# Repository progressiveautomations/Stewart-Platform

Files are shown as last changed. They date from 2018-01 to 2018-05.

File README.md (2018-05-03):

# Stewart Platform

## Table of Contents
[Quick Start Guide](#qsg)

[Wiring the Electronics](#wiring)

[Mechanical Assembly](#mech)

[Troubleshooting](#ts)

<a name="qsg"/>

# Quick Start Guide
1. Ensure that power to the platform is turned off, the USB cable from the platform is unplugged from the computer, and all GUI instances are closed.
2. (if Leap Motion is to be used) Ensure that the Leap Motion service and software is started, and the controller is plugged into the computer.
3. Turn on the power to the platform, and plug the USB cable from the platform into the computer.
4. Launch the GUI; in the 'Options' menu, click "Select COM Port".
5. Find the COM port corresponding to the Arduino Due (should show up in the Device Description on the left hand side, as shown), and change the baud rate to 115200.
6. Click connect, and the platform should immediately begin its calibration routine by moving all actuators to full extension, and retracting to minimum position. DO NOT SEND ANY COMMANDS TO THE PLATFORM DURING THIS PHASE!
7. Check the beginning of the log to ensure calibration has succeeded.
8. Manually control the actuators by moving the sliders and/or entering values into the corresponding textbox. To enable Leap Motion, ensure its status is "Connected", and tick the "Enable Leap Motion" checkbox above the sliders.

# Assembly Instructions

<a name="wiring"/>

## Wiring the Electronics

Before assembly, ensure that all the wires are adequately connected within the enclosure, including the power supply wires, the actuator power wires, the actuator signal wires, and the Arduino Due wires. Detail in [how the components are wired together](electronics/electronics_layout.pdf) and individual schematics are located in the `electronics` folder.

To ensure the code under `arduino/platform` is compatible with the wiring of the Arduino Due, the headers on the PCB should be connected to the respective pins in the table below. This assumes actuators 1 through 3 are connected to Multimoto 1 (to blocks M3, M2, and M1 respectively) and actuators 4 through 6 similarly to Multimoto 2. Note the actuator indexing for the PCBs differs from that in software.
- The indexing on the PCBs are ordered by the motor blocks on the Multimoto boards. Indices 1 through 4 correspond to M1 through M4 on Multimoto 1, and the same for indices 5 though 8 with Multimoto 2.
- The indexing in software is ordered by how the signal wires interface with the PCB terminal blocks. This should match the order (left to right) in which they are connected to the enclosure ports.

The UTIL pin headers (RESET, +3.3V, +5V, GND, GND, Vin) are connected to the identically-named Arduino pins and are omitted from this list. The exact pin numbering can be updated in software at `arduino/platform/pin_layout.h` if the wiring configuration needs to be modified.

| Header | Pin |
|---|----:|
| POT_1 |  A6 |
| POT_2 |  A7 |
| POT_3 |  A8 |
| POT_4 |  A9 |
| POT_5 | A10 |
| POT_6 | A11 |
| DIR_1 |  41 |
| DIR_2 |  39 |
| DIR_3 |  37 |
| DIR_5 |  35 |
| DIR_6 |  33 |
| DIR_7 |  31 |
| PWM_1 |  13 |
| PWM_2 |  12 |
| PWM_3 |  11 |
| PWM_5 |  10 |
| PWM_6 | 9 |
| PWM_7 | 8 |
| ENABLE_1 |  24 |
| ENABLE_2 |  25 |

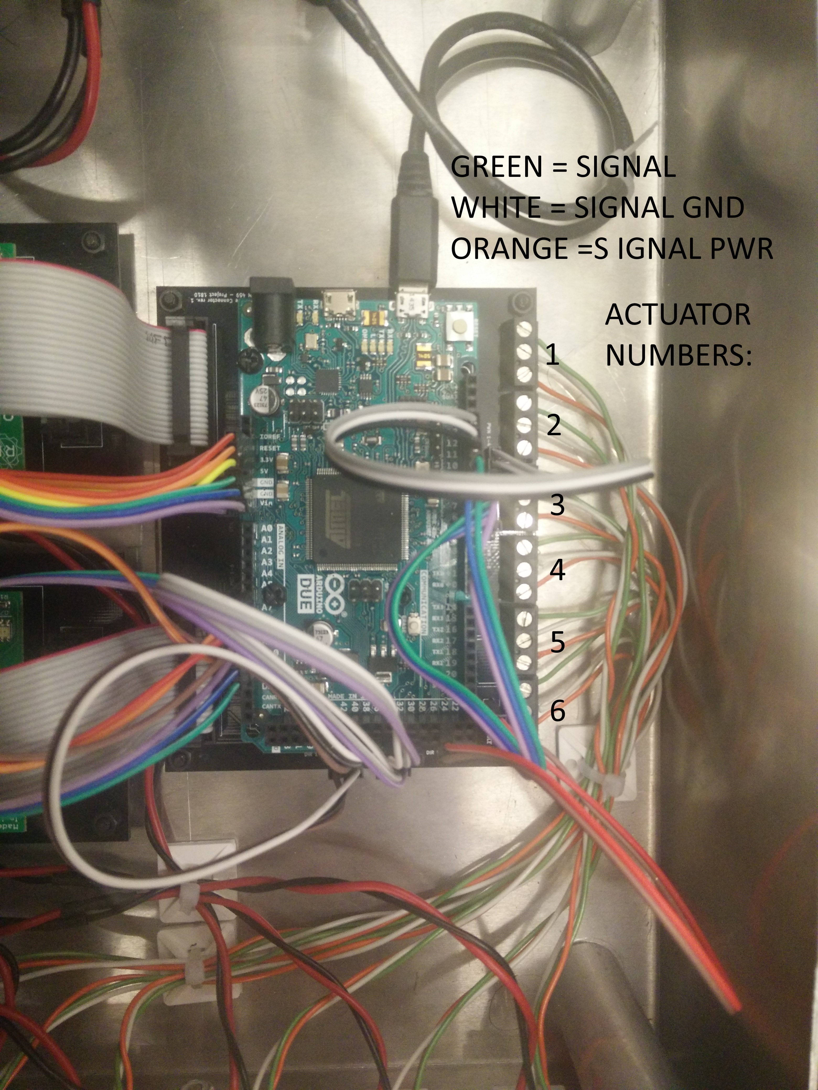
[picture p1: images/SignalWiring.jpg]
Picture of Arduino I/O wiring

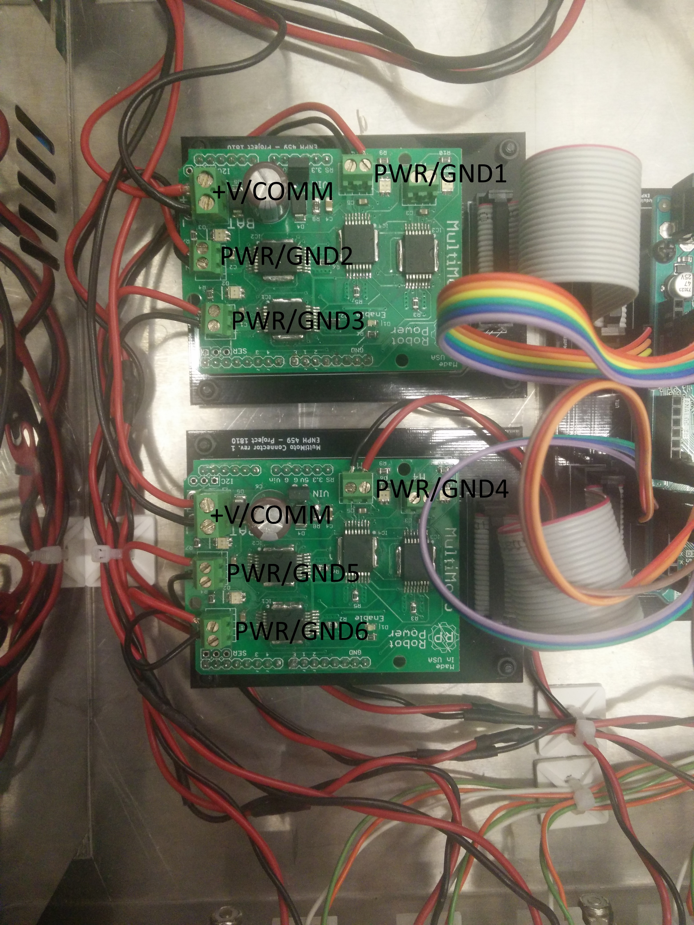
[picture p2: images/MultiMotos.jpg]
Picture of MultiMoto wiring


<a name="mech"/>

## Mechanical Assembly

Attach the 3 platform legs to the 3 corners of the base plate (Note: the base plate is larger than the top plate, and has 4 slots cut into it.), such that the 6 metal flanges are facing upwards. This is done using the ¾” long, ⅜”-16 threaded bolts, with one washer.

Picture of base leg

Next, position the enclosure underneath the base, so that the enclosure posts align with the slots in the base plate, with the power and USB connectors facing out as shown.

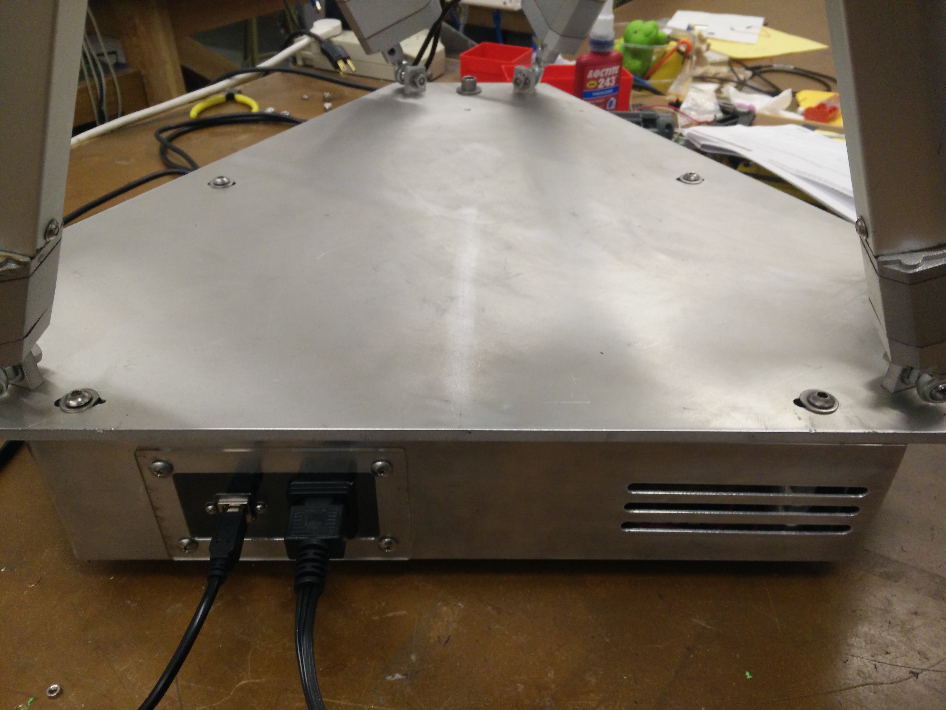
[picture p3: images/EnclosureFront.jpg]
Enclosure picture


Attach the enclosure to the base place using 4 1” long,  ¼”-20 threaded bolts, with a washer for each. Ensure the bolts are aligned in the slots such that the corners of the enclosure do not extend beyond the edge of the base plates, like shown.

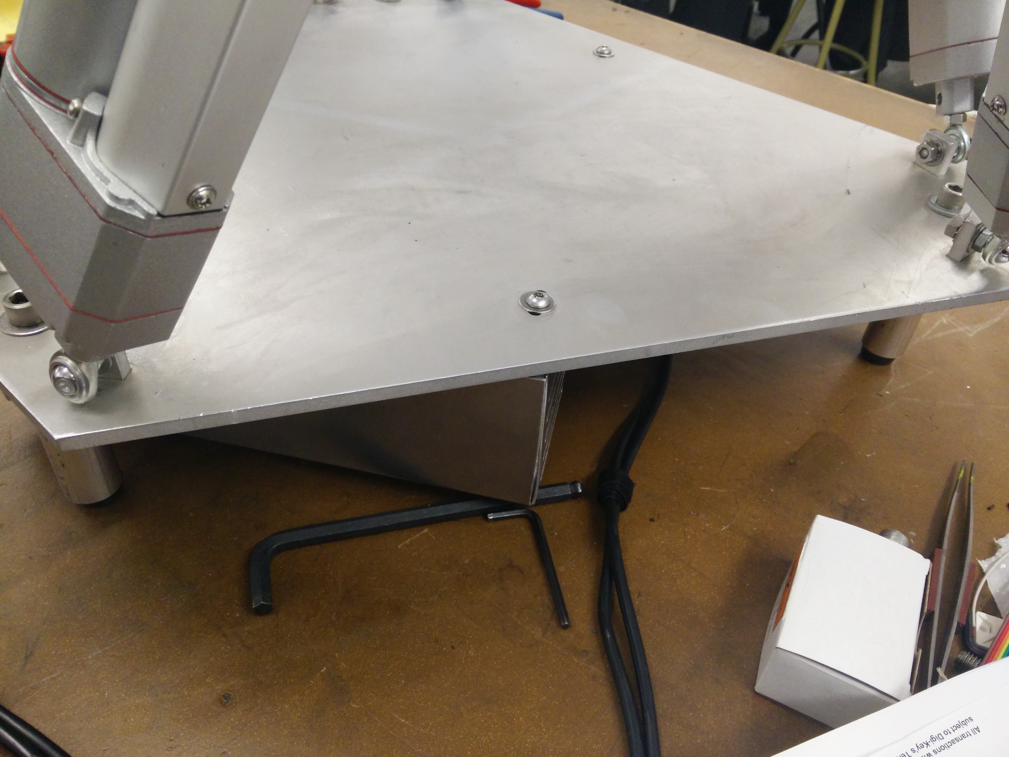
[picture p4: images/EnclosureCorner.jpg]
Enclosure corner


Attach the actuators as shown in the following picture. Close-up views of the joints are provided. Use 2 washers (one on each side), a lock-washer, and a ¼”-28 nut.

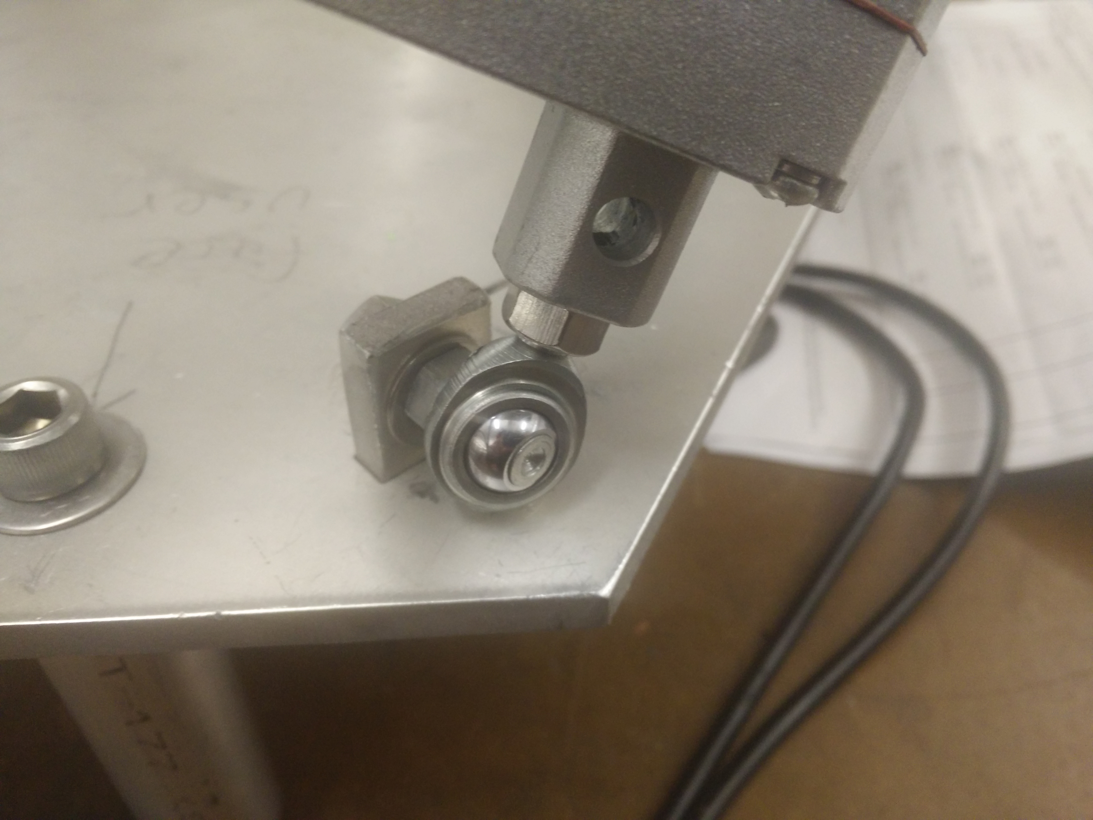
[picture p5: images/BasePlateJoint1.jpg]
Joint picture 1


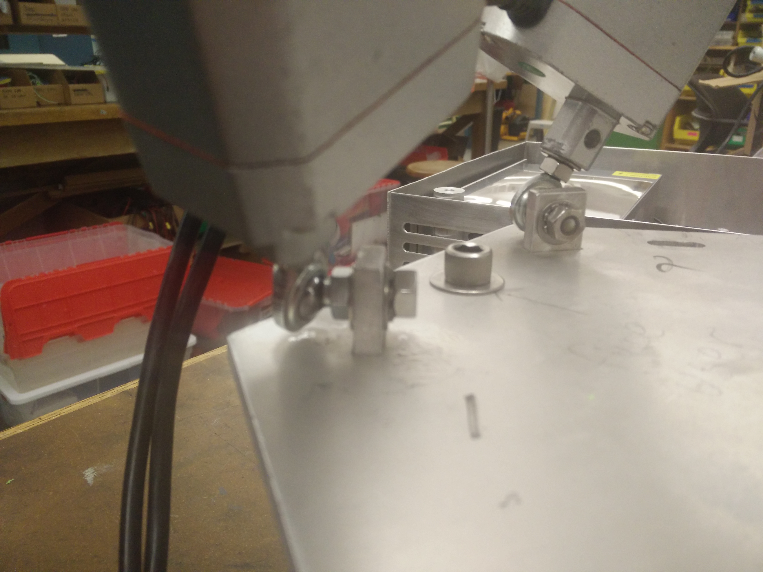
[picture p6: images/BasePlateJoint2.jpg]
Joint picture 2


To avoid problems, ensure that the actuator gearboxes are facing upwards as shown in the picture.

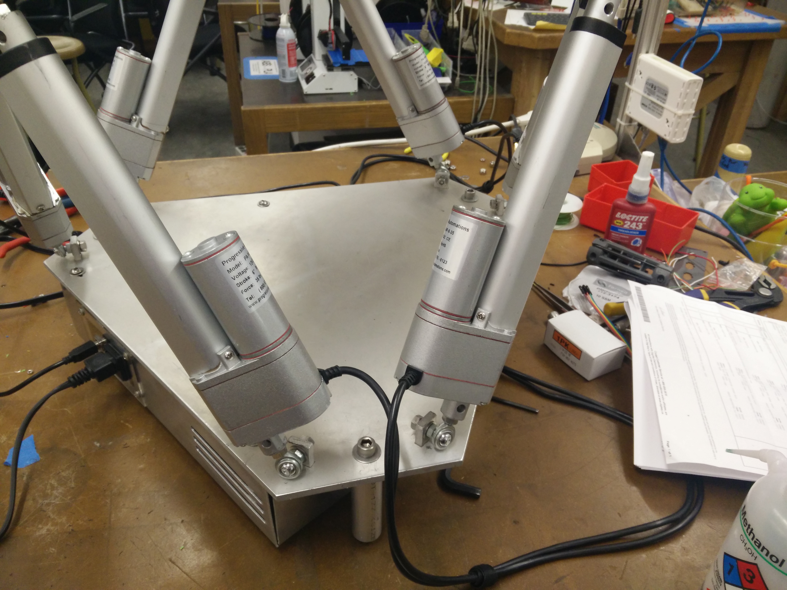
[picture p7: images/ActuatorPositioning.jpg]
Picture of actuator positions


Once the platform is assembled, attach the maze to the top plate by aligning the 3 corner holes on each, and secure it with 3 1¼” long, ⅜”-16 threaded bolts, with one washer on each, and a nut.

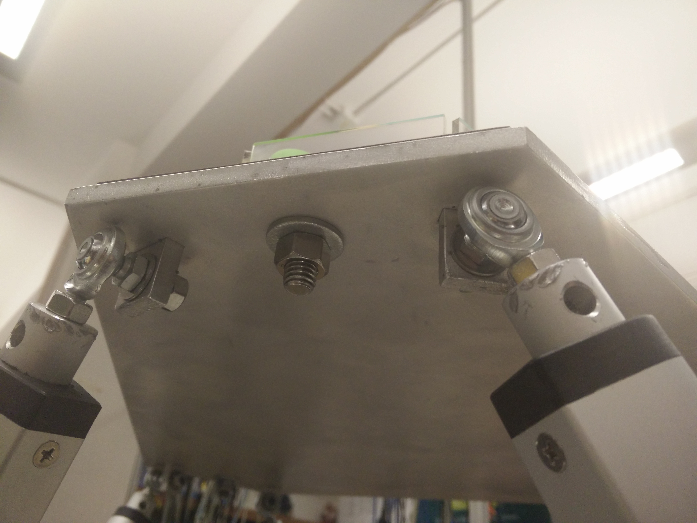
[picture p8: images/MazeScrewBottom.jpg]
Maze bolt pic 1

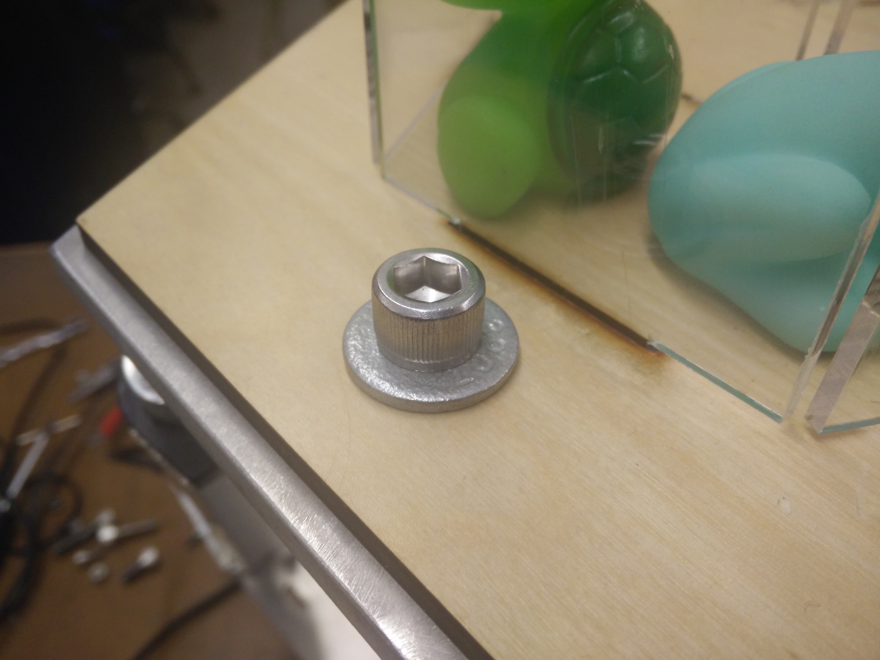
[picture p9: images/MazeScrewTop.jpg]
Maze bolt pic 2


Connect all the actuator connectors to the appropriate receptacles on the enclosure, by routing the cables around and under the base plate. These can be bundled to be neat and out-of-view.

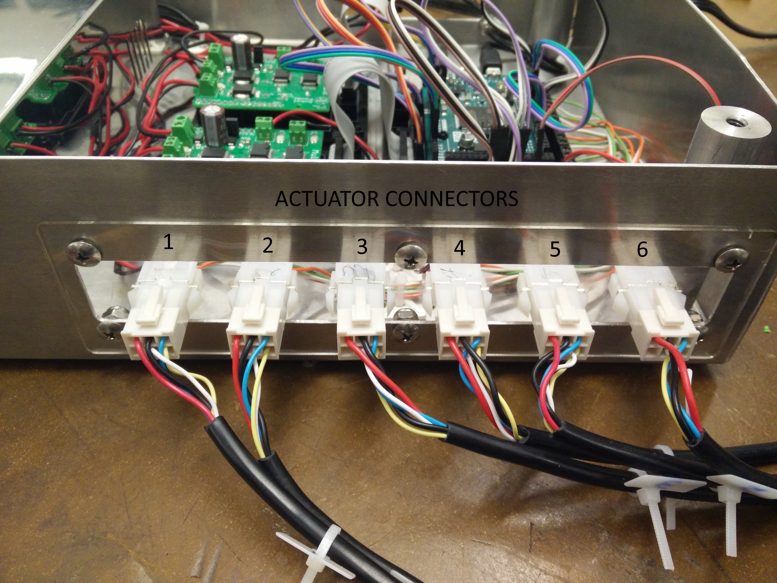
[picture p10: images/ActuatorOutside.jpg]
Pic of cables and connectors


Finally, connect the power and USB cables to the front of the enclosure, and connect the other end of the USB cable. The platform is now assembled!

<a name="ts"/>

# Troubleshooting

Nothing is moving? Check all power connectors.

Arduino not seen by computer? Check USB cable connection, and ensure the device shows up in Device Manager.

Noisy actuator readings? Adjust the PWM feedback or the filtering capacitances on the Arduino PCB.

## PCB design
The PCBs were designed using [KiCAD v4.0.7](http://kicad-pcb.org/).

Each board has its design files under the `electronics` folder, along with Gerber files (under `electronics/gerber`) for the case of reproduction. The individual netlists can be found in the `.sch` files.

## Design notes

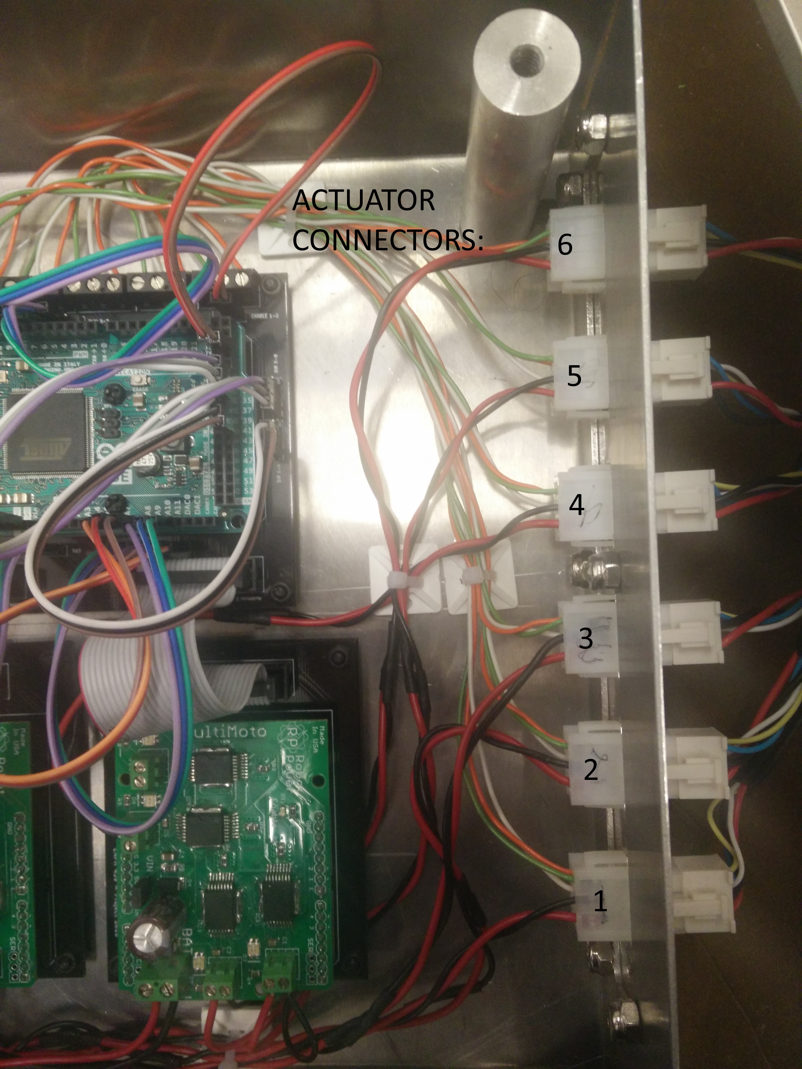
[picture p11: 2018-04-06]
images/ActuatorConnectors.jpg

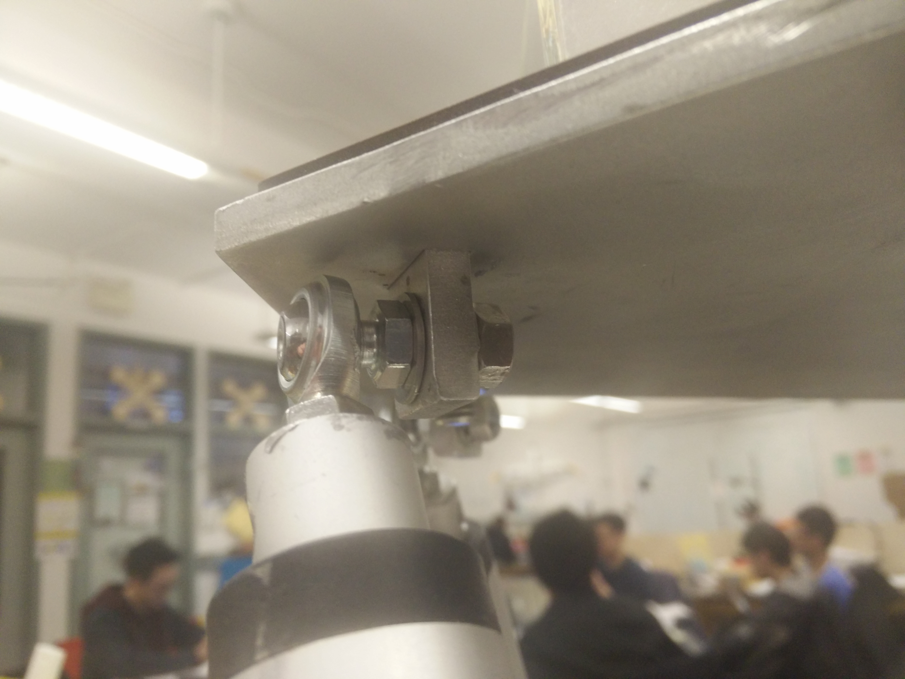
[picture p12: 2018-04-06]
images/TopPlateJoint2.jpg

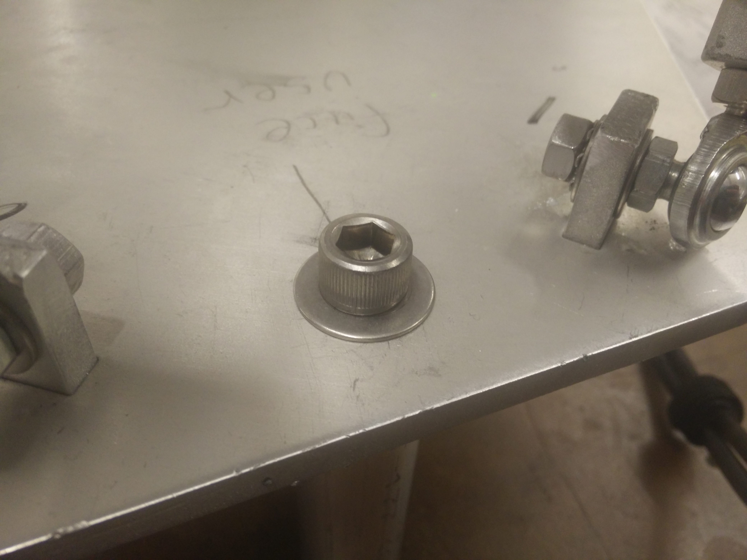
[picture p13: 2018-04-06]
images/BaseScrew.jpg

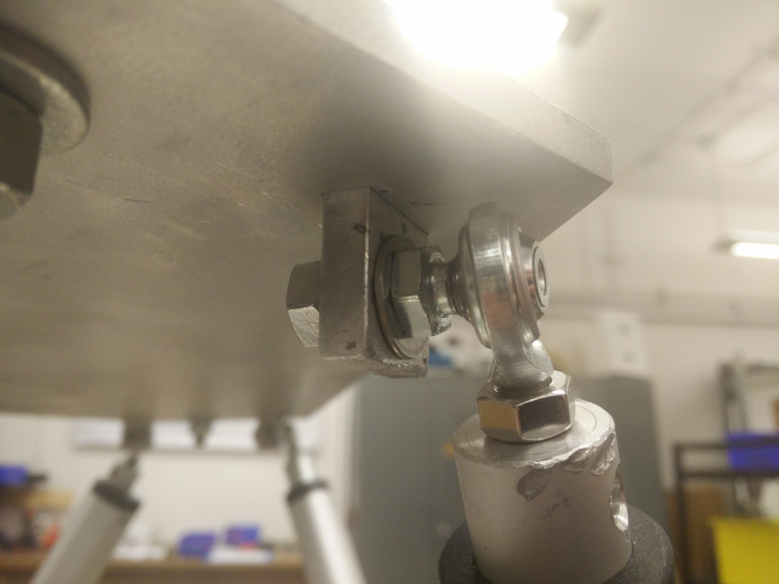
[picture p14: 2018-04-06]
images/TopPlateJoint.jpg

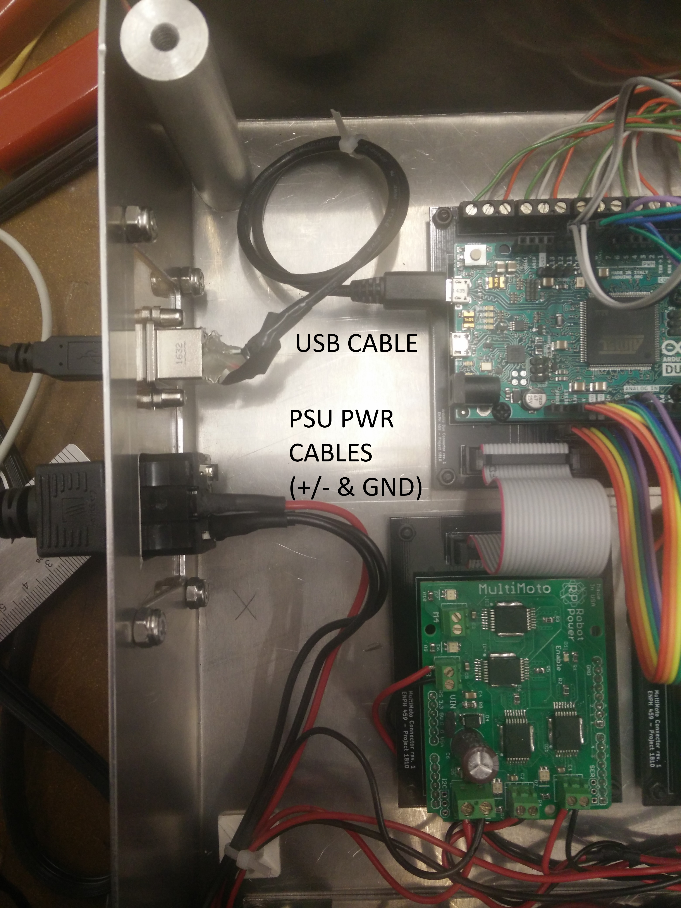
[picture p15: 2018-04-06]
images/USB-PWR.jpg

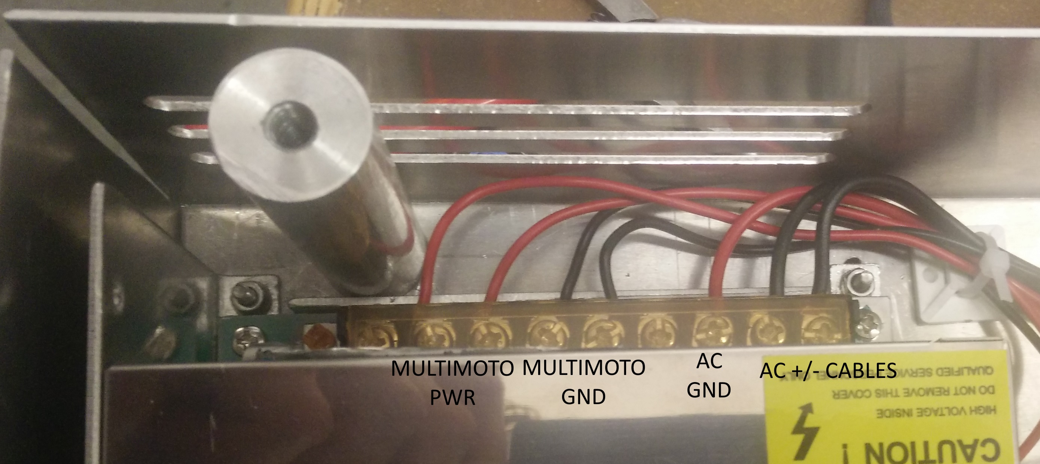
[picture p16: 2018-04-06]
images/PSUCables.jpg

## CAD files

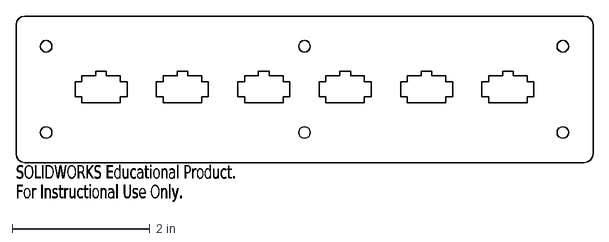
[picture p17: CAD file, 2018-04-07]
mechanical/MotorPanel2.DXF
SOLIDWORKS Educational Product.
For Instructional Use Only.

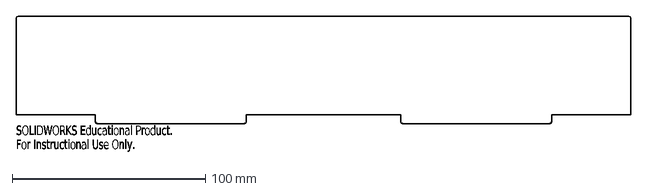
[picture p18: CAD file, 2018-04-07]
mechanical/TiltMazeWallLarge.DXF
SOLIDWORKS Educational Product.
For Instructional Use Only.

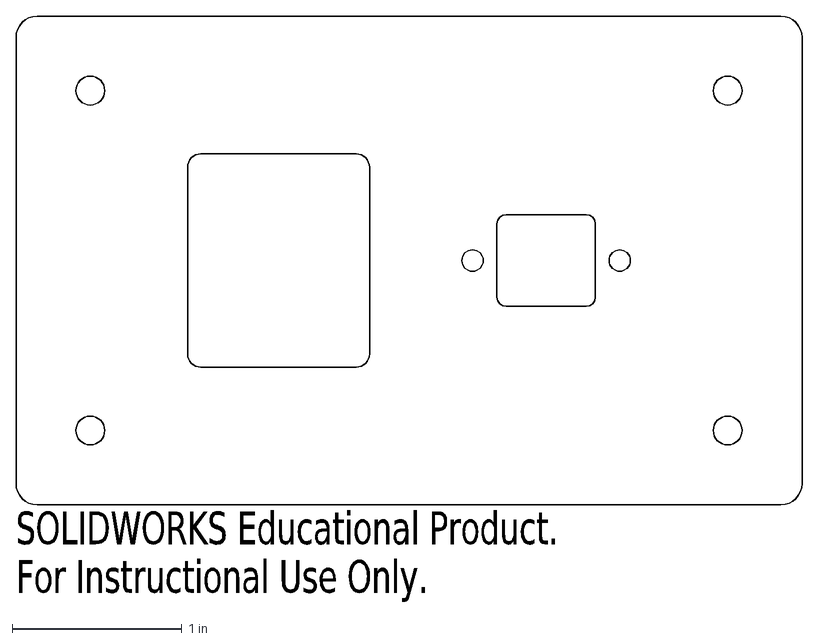
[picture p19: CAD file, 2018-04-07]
mechanical/PowerUSBPanel2.DXF
SOLIDWORKS Educational Product.
For Instructional Use Only.

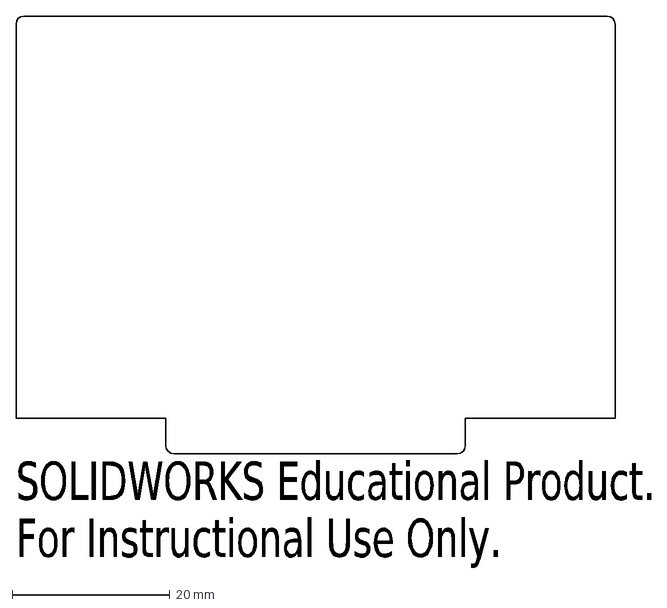
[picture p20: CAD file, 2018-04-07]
mechanical/TiltMazeWallSmall.DXF
SOLIDWORKS Educational Product.
For Instructional Use Only.

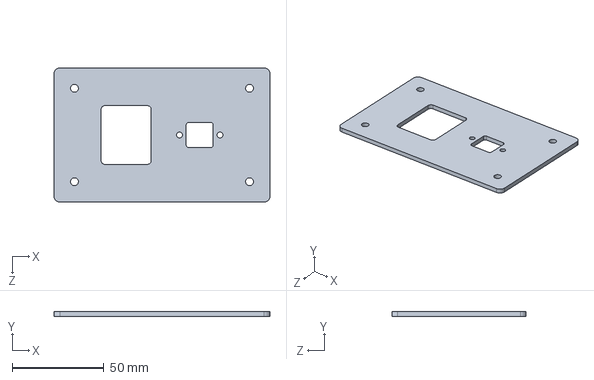
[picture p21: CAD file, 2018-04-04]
mechanical/PowerUSBPanel.SLDPRT
117.5 x 2.54 x 73.0 mm

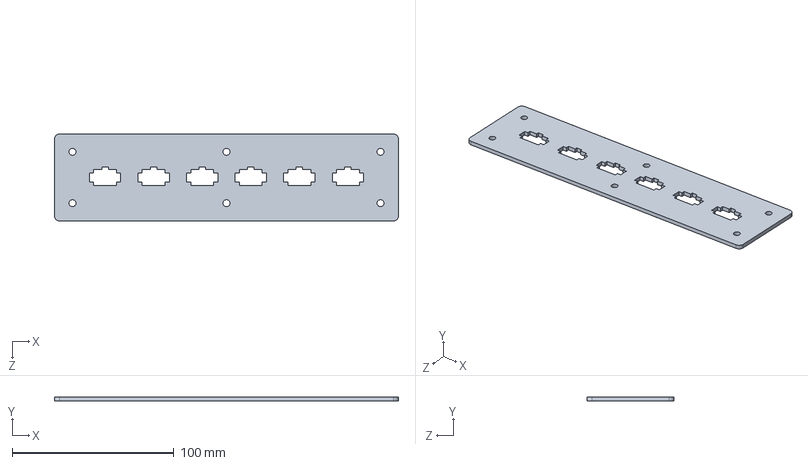
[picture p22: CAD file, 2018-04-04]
mechanical/MotorPanel.SLDPRT
212.7 x 2.54 x 54.0 mm

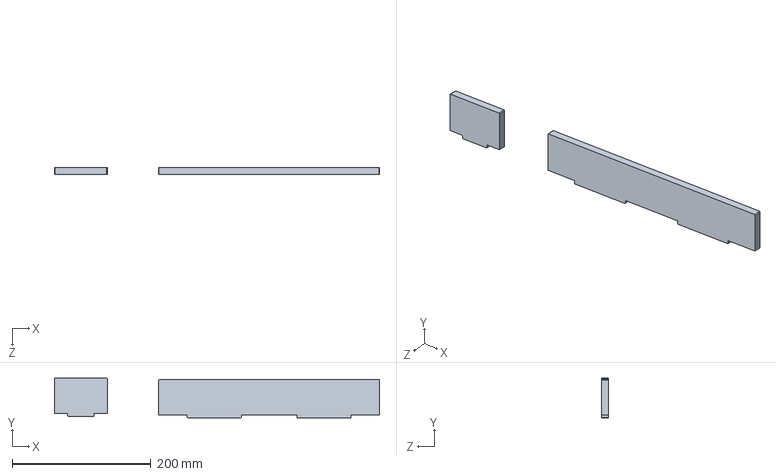
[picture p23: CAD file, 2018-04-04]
mechanical/TiltMazeWalls.SLDPRT
468.1 x 57.6 x 10.0 mm

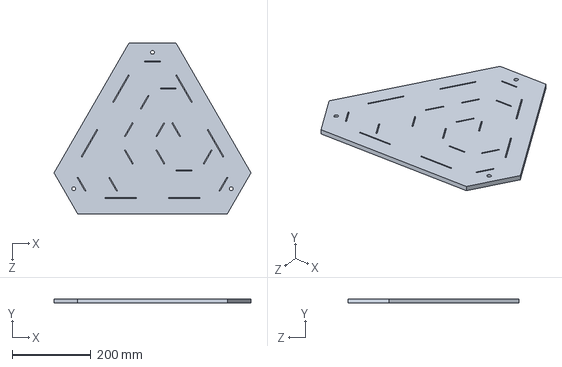
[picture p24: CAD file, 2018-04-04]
mechanical/TiltMaze1.SLDPRT
500.0 x 10.0 x 433.0 mm

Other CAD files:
mechanical/PlatformPlates.SLDPRT
mechanical/MotorPanel.SLDDRW
mechanical/PlatformPlates.SLDDRW
mechanical/PowerUSBPanel.SLDDRW
mechanical/TiltMaze1.DXF
mechanical/TiltMazeBase.SLDDRW
mechanical/TiltMazeWalls.SLDDRW

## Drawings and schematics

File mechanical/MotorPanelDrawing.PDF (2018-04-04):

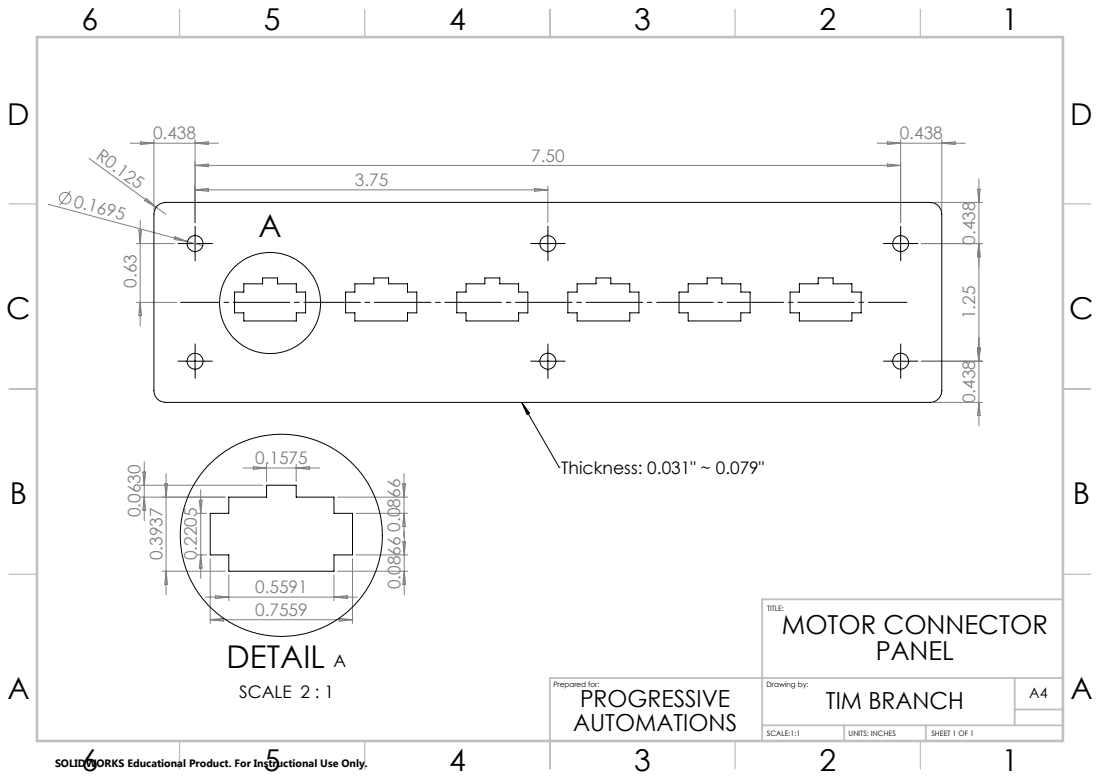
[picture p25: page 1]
Thickness: 0.031" ~ 0.079"; DETAIL A; SCALE 2 : 1; Drawing by:; SCALE:1:1; SHEET 1 OF 1; MOTOR CONNECTOR; TIM BRANCH; Prepared for:; AUTOMATIONS; UNITS: INCHES

SOLIDWORKS Educational Product. For Instructional Use Only.

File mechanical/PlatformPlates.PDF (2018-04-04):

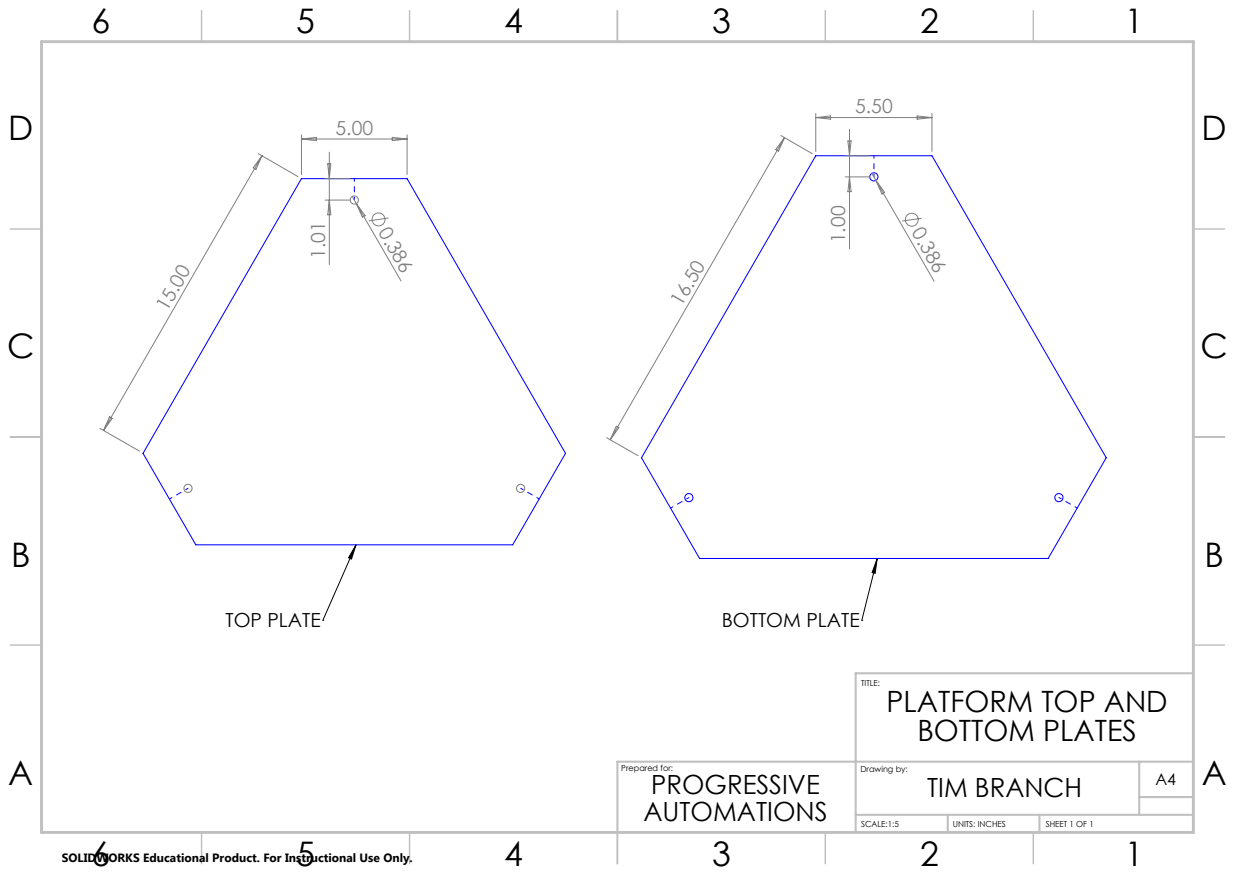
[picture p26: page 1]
TOP PLATE; BOTTOM PLATE; Drawing by:; SCALE:1:5; SHEET 1 OF 1; Prepared for:; AUTOMATIONS; UNITS: INCHES

TITLE:
PLATFORM TOP AND
BOTTOM PLATES
TIM BRANCH

SOLIDWORKS Educational Product. For Instructional Use Only.

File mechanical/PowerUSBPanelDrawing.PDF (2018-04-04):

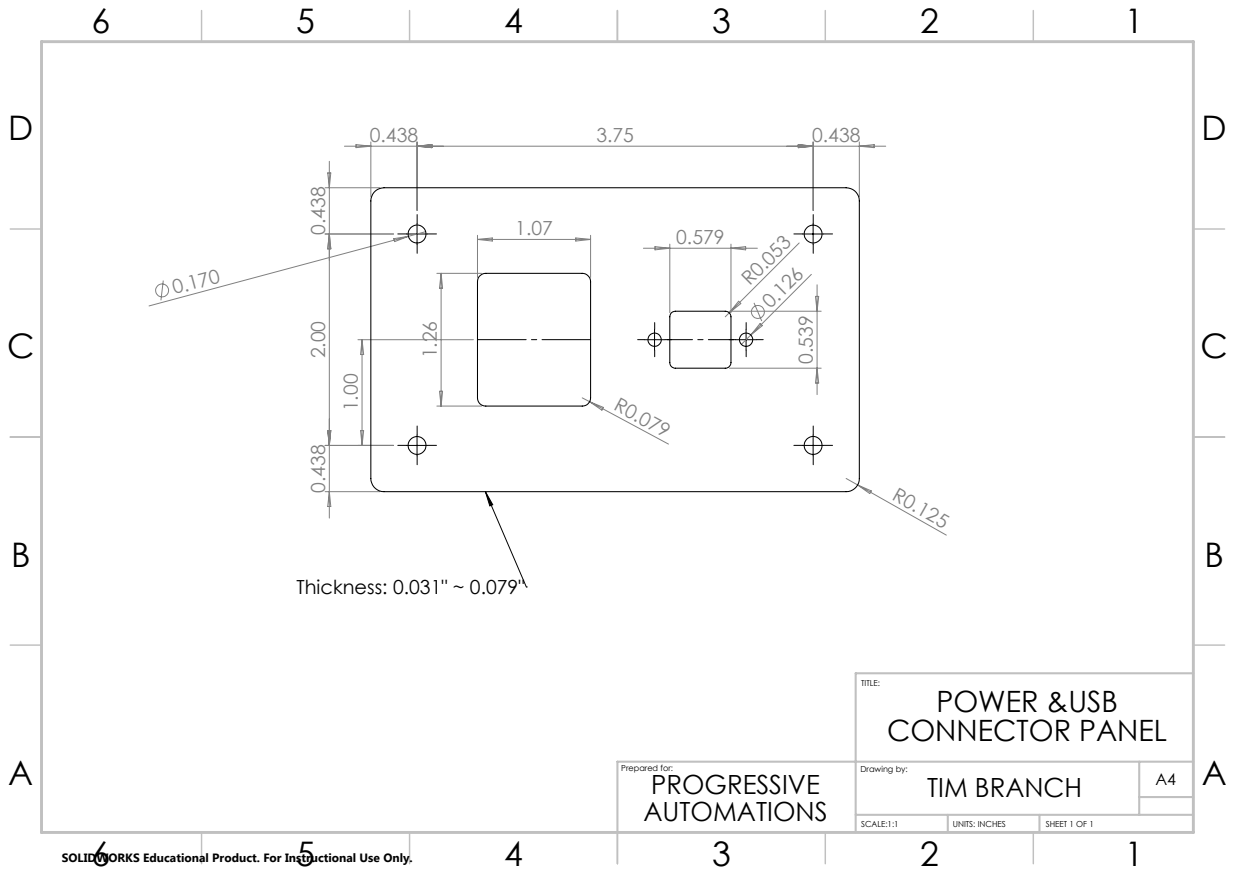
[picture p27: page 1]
Thickness: 0.031" ~ 0.079"; Drawing by:; SCALE:1:1; SHEET 1 OF 1; POWER &USB CONNECTOR PANEL; TIM BRANCH; Prepared for:; AUTOMATIONS; UNITS: INCHES

SOLIDWORKS Educational Product. For Instructional Use Only.

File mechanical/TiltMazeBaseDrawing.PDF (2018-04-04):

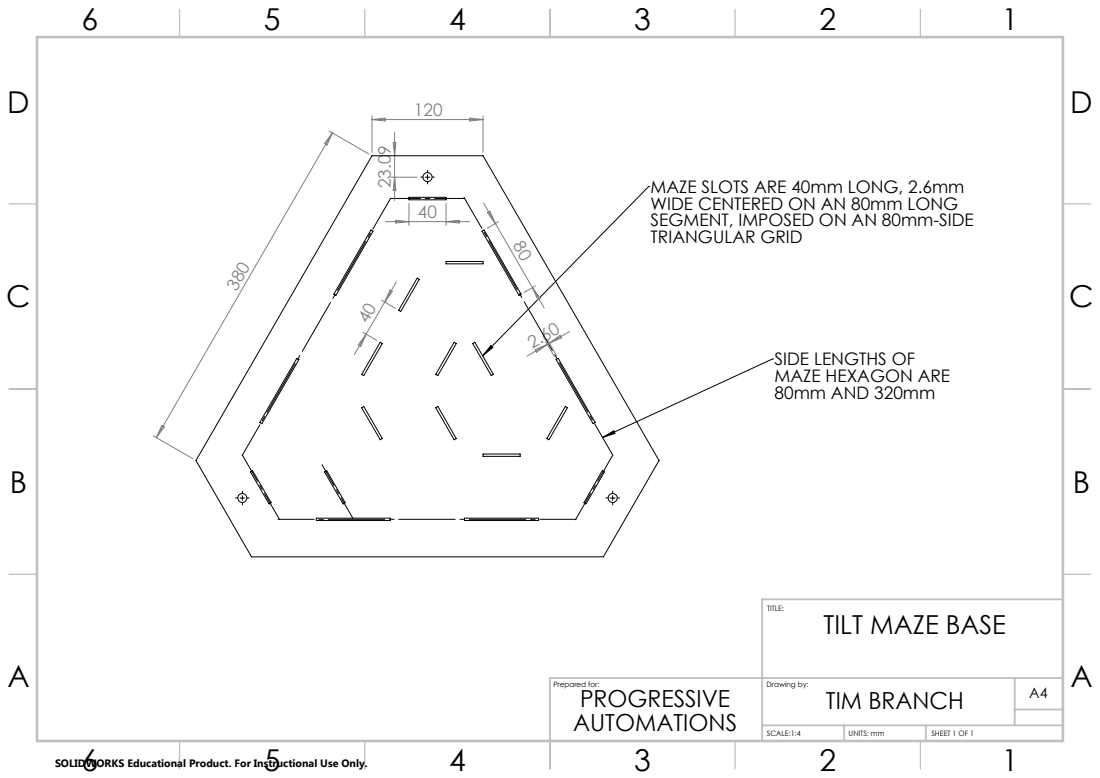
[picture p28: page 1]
Drawing by:; SCALE:1:4; SHEET 1 OF 1; TIM BRANCH; Prepared for:; AUTOMATIONS; UNITS: mm

MAZE SLOTS ARE 40mm LONG, 2.6mm
WIDE CENTERED ON AN 80mm LONG
SEGMENT, IMPOSED ON AN 80mm-SIDE
TRIANGULAR GRID

SIDE LENGTHS OF
MAZE HEXAGON ARE
80mm AND 320mm

TITLE:
TILT MAZE BASE

SOLIDWORKS Educational Product. For Instructional Use Only.

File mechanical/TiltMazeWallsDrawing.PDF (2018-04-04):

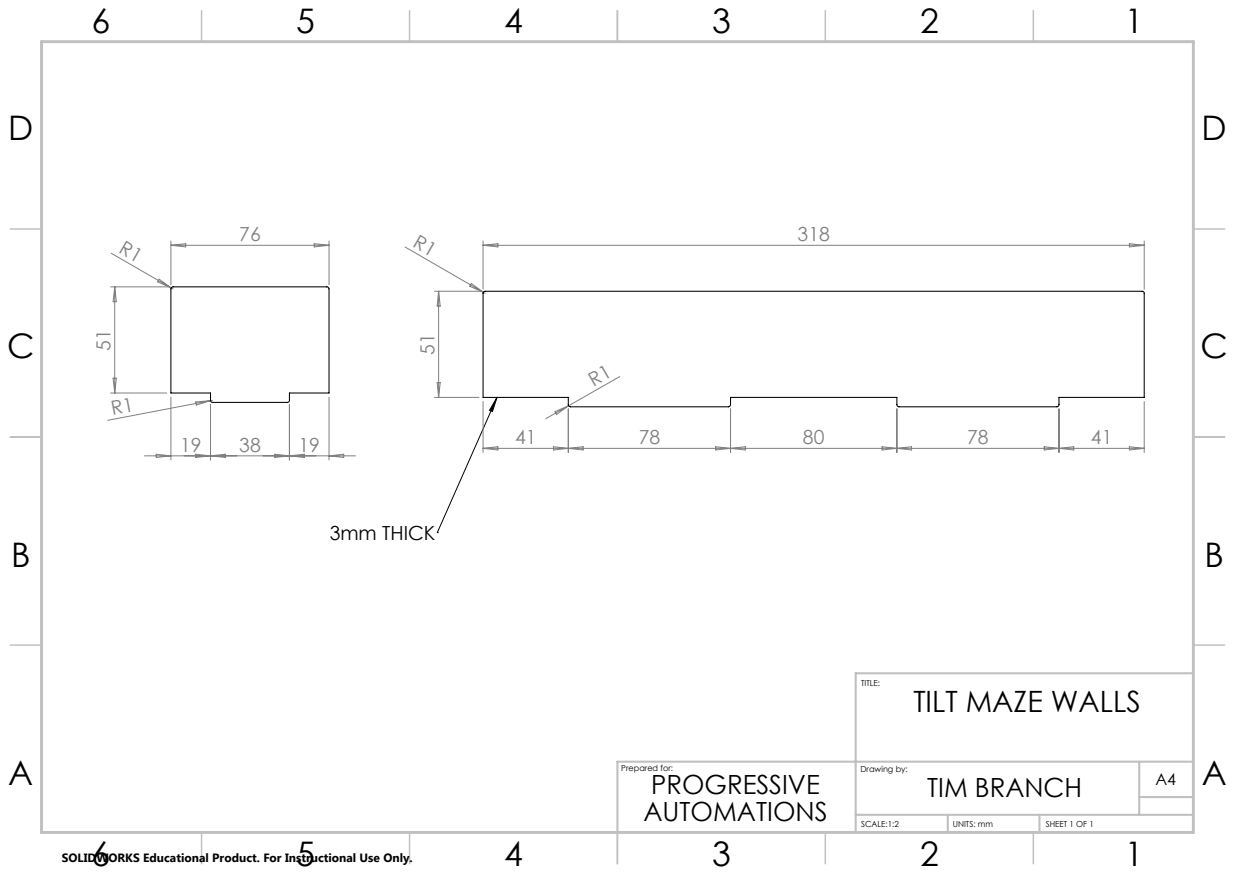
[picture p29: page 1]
3mm THICK; Drawing by:; SCALE:1:2; SHEET 1 OF 1; TIM BRANCH; Prepared for:; AUTOMATIONS; UNITS: mm

TITLE:
TILT MAZE WALLS

SOLIDWORKS Educational Product. For Instructional Use Only.

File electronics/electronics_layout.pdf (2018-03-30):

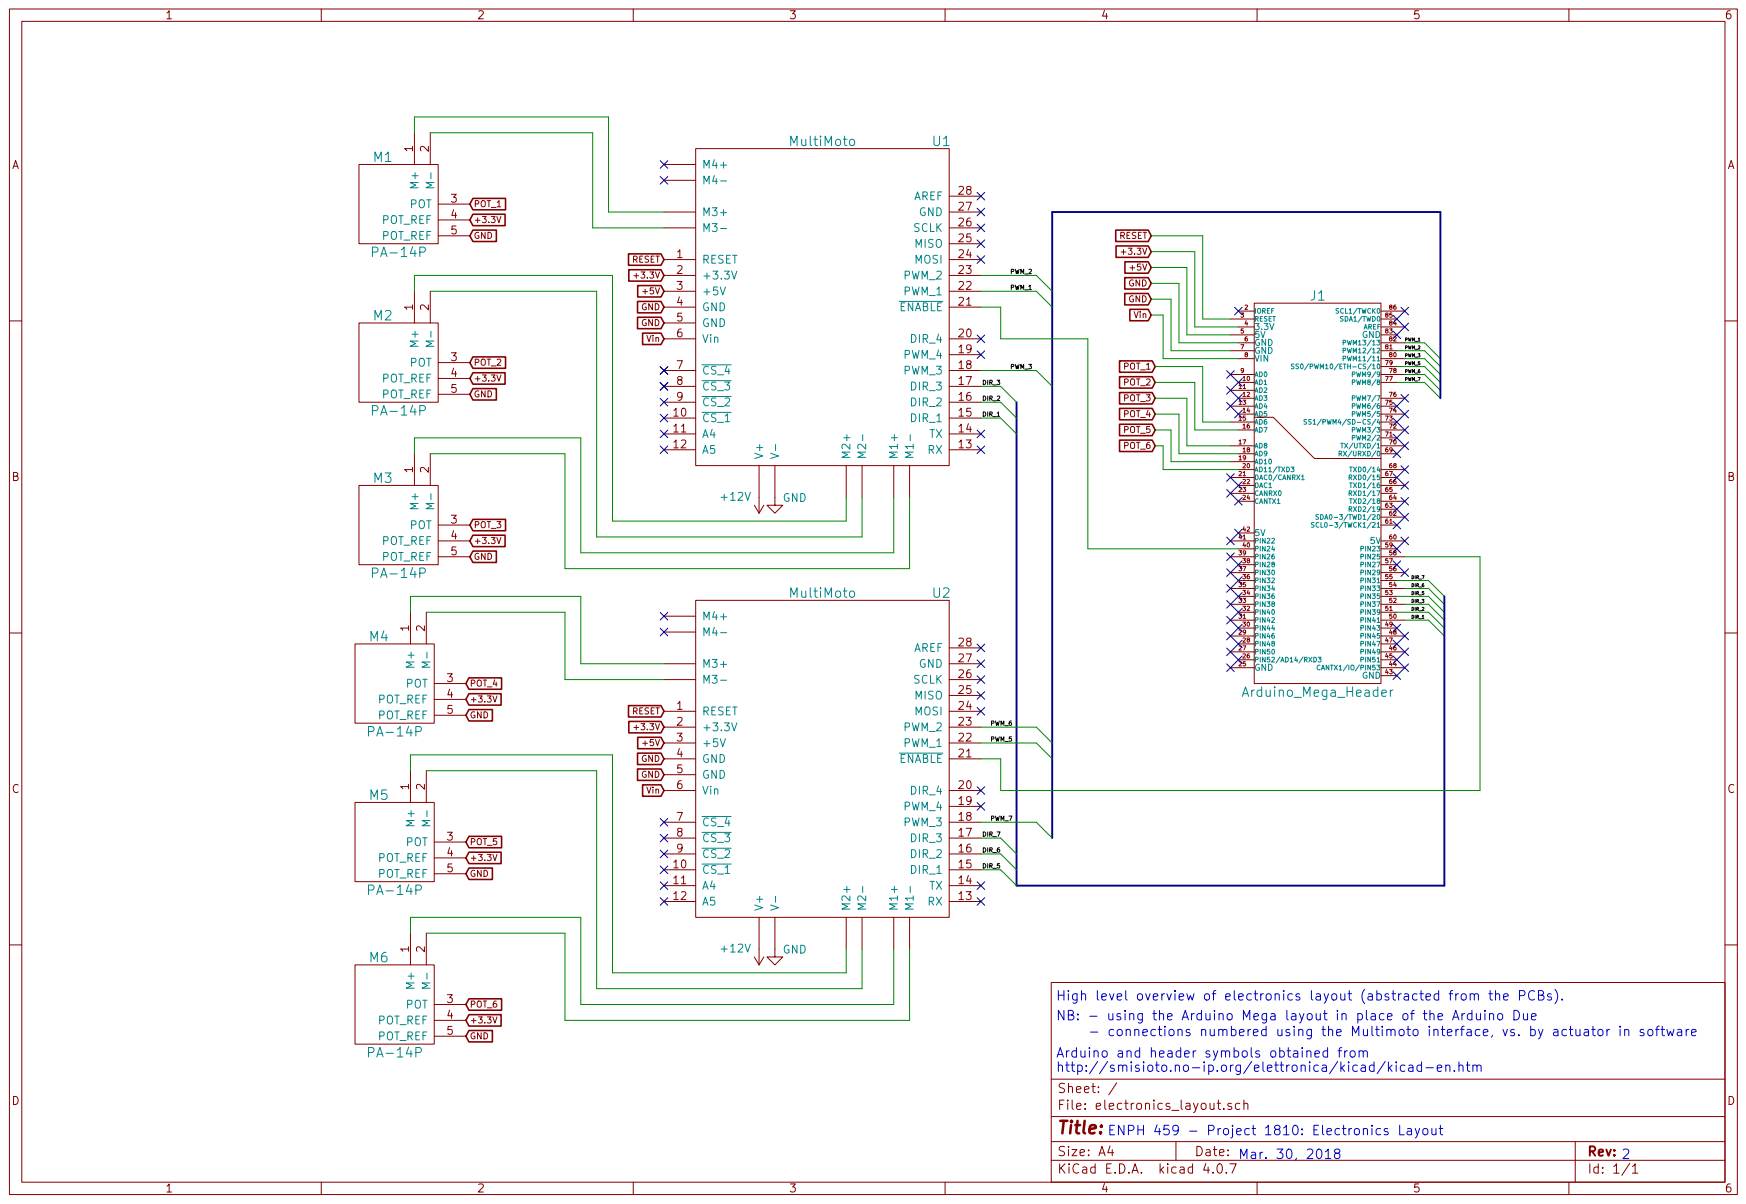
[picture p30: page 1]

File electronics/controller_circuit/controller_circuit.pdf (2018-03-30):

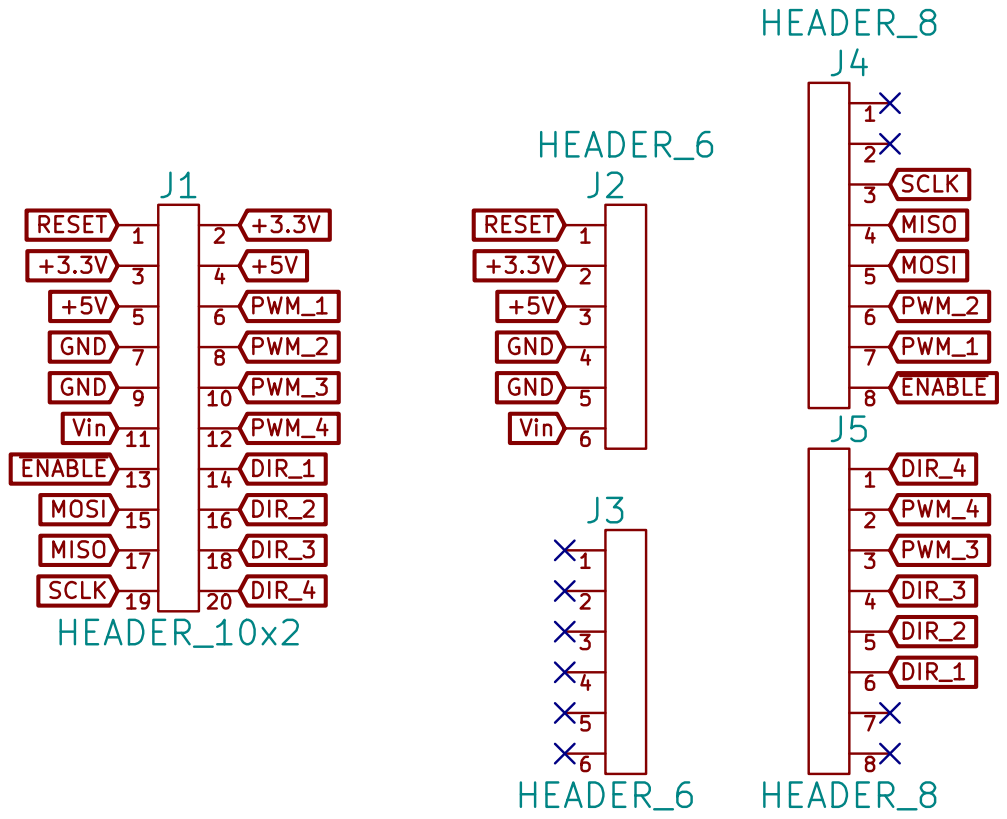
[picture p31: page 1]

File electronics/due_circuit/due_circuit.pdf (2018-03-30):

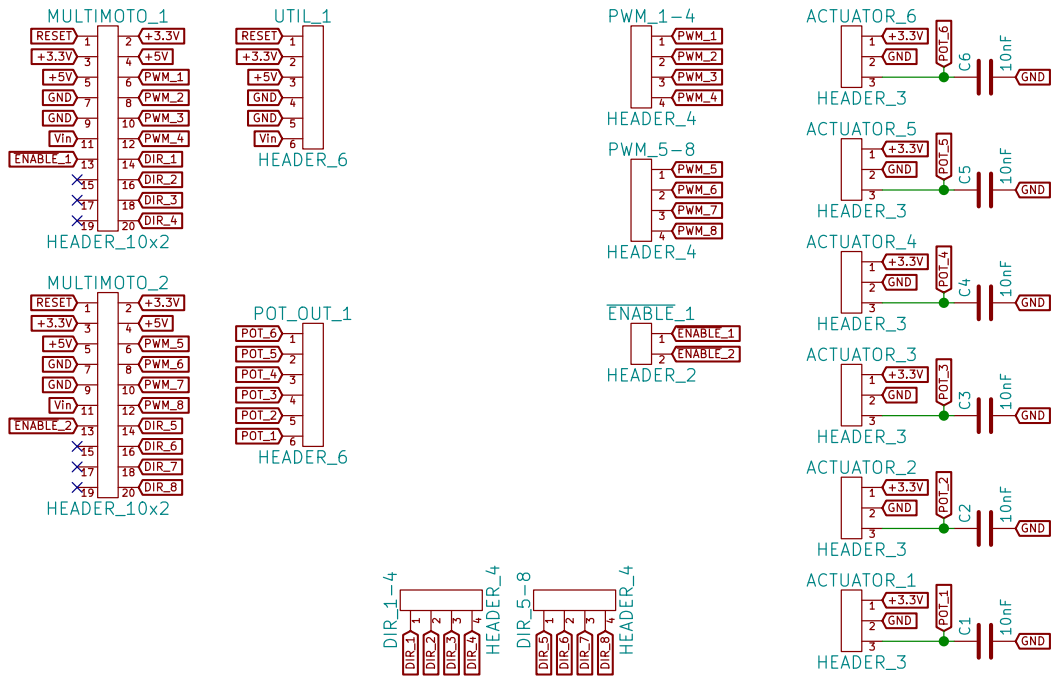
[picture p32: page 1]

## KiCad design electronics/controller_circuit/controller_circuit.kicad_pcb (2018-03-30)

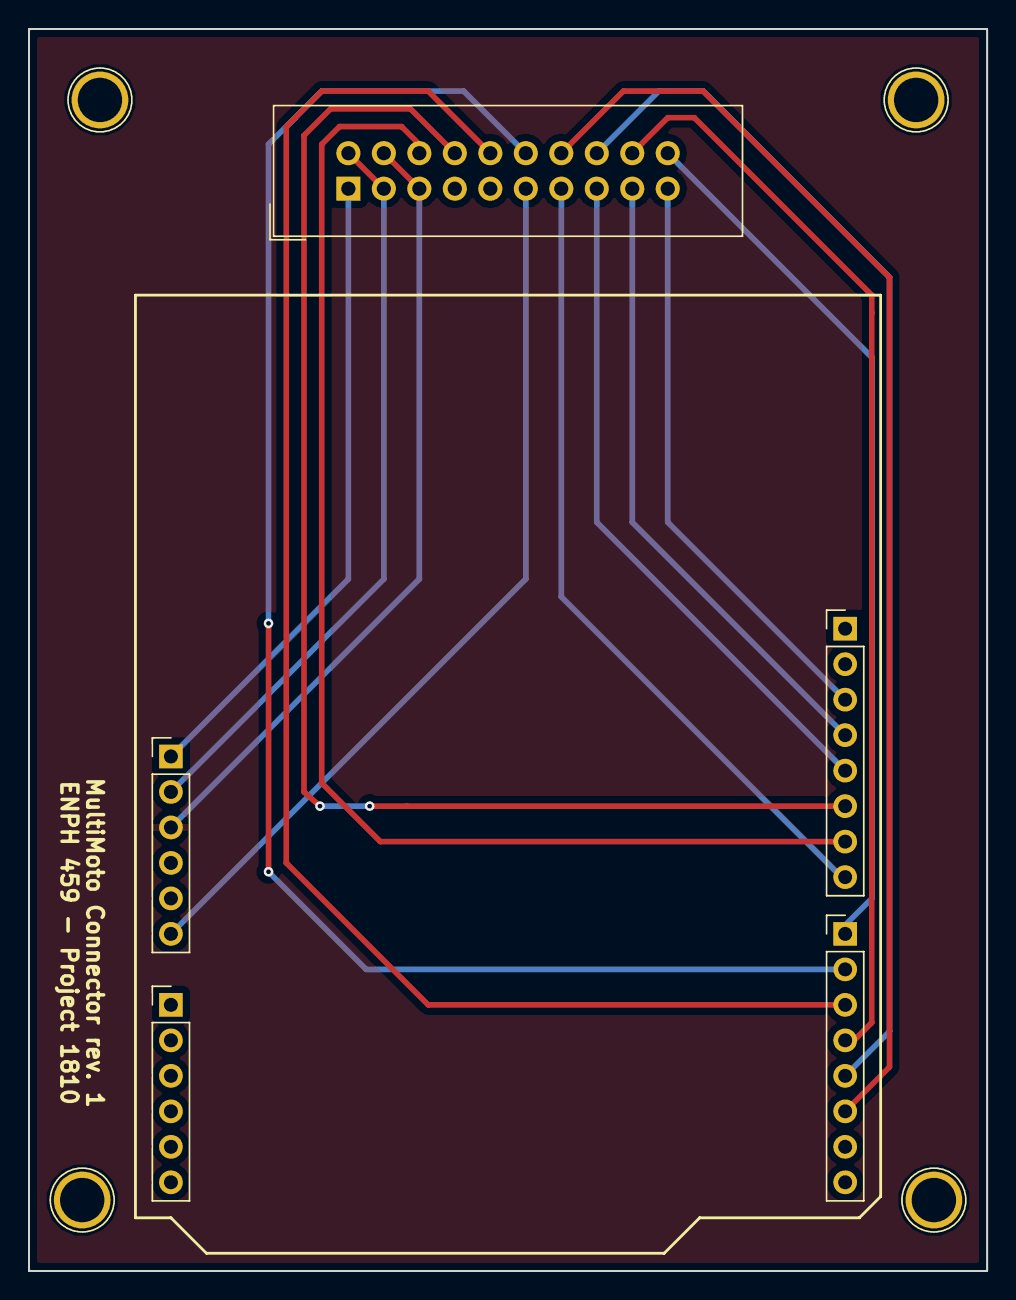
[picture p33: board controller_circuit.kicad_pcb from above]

Board: 2 copper layers, 68.6 x 88.9 mm, 5 parts (0 on the bottom side), 17 nets.

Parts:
J1: HEADER_10x2; IDC-Header_2x10_Pitch2.54mm_Straight
J2, J3: HEADER_6; Socket_Strip_Straight_1x06_Pitch2.54mm
J4, J5: HEADER_8; Socket_Strip_Straight_1x08_Pitch2.54mm

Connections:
+3.3V: J1.2, J1.3, J2.2
+5V: J1.4, J1.5, J2.3
DIR_1: J1.14, J5.6
DIR_2: J1.16, J5.5
DIR_3: J1.18, J5.4
DIR_4: J1.20, J5.1
GND: J1.7, J1.9, J2.4, J2.5
MISO: J1.17, J4.4
MOSI: J1.15, J4.5
PWM_1: J1.6, J4.7
PWM_2: J1.8, J4.6
PWM_3: J1.10, J5.3
PWM_4: J1.12, J5.2
RESET: J1.1, J2.1
SCLK: J1.19, J4.3
Vin: J1.11, J2.6
~ENABLE~: J1.13, J4.8

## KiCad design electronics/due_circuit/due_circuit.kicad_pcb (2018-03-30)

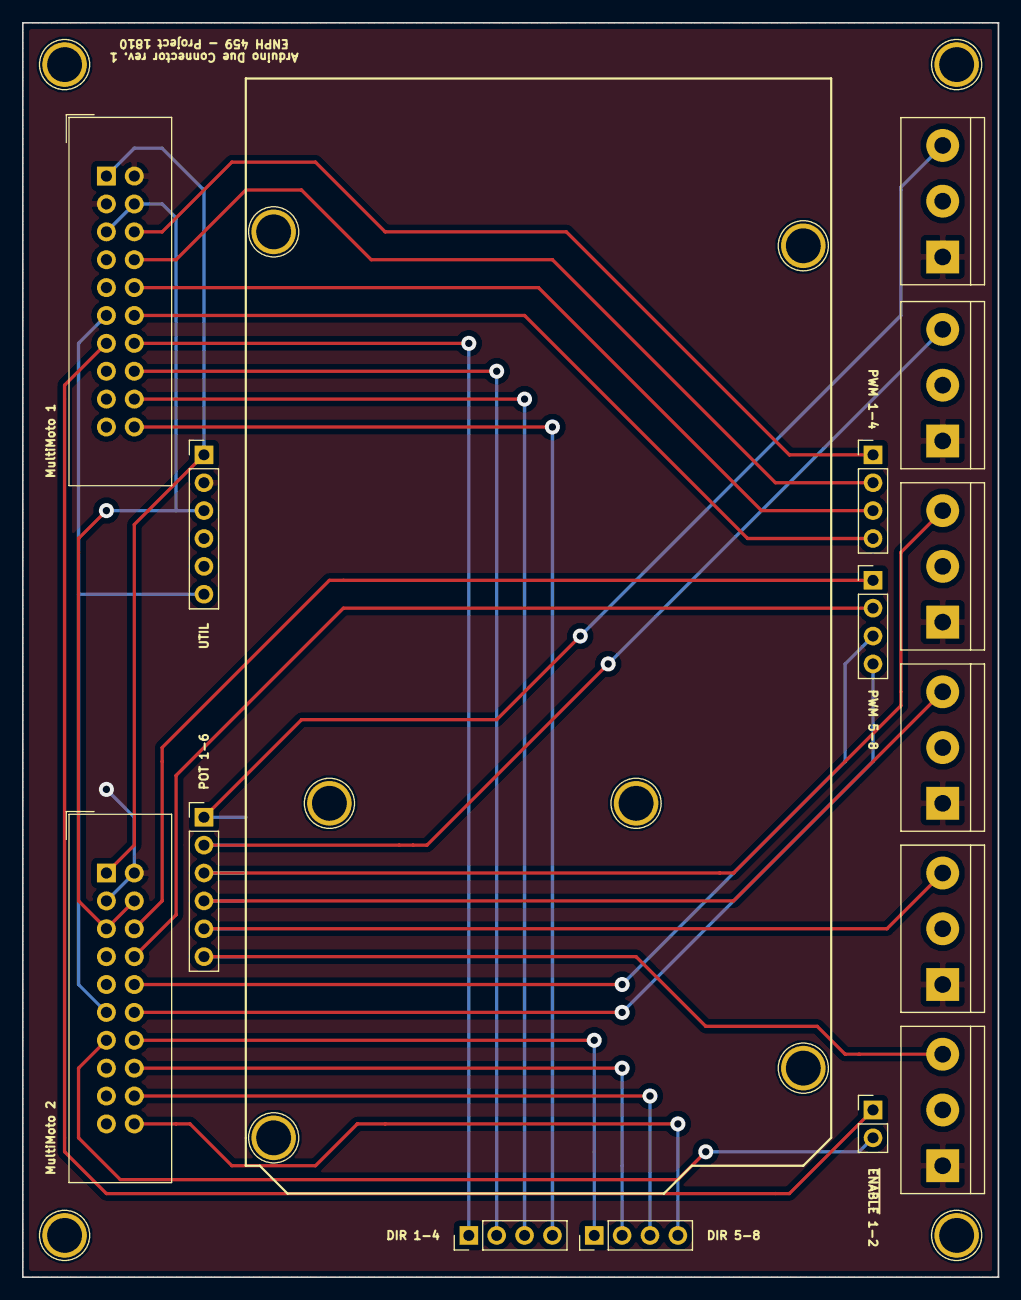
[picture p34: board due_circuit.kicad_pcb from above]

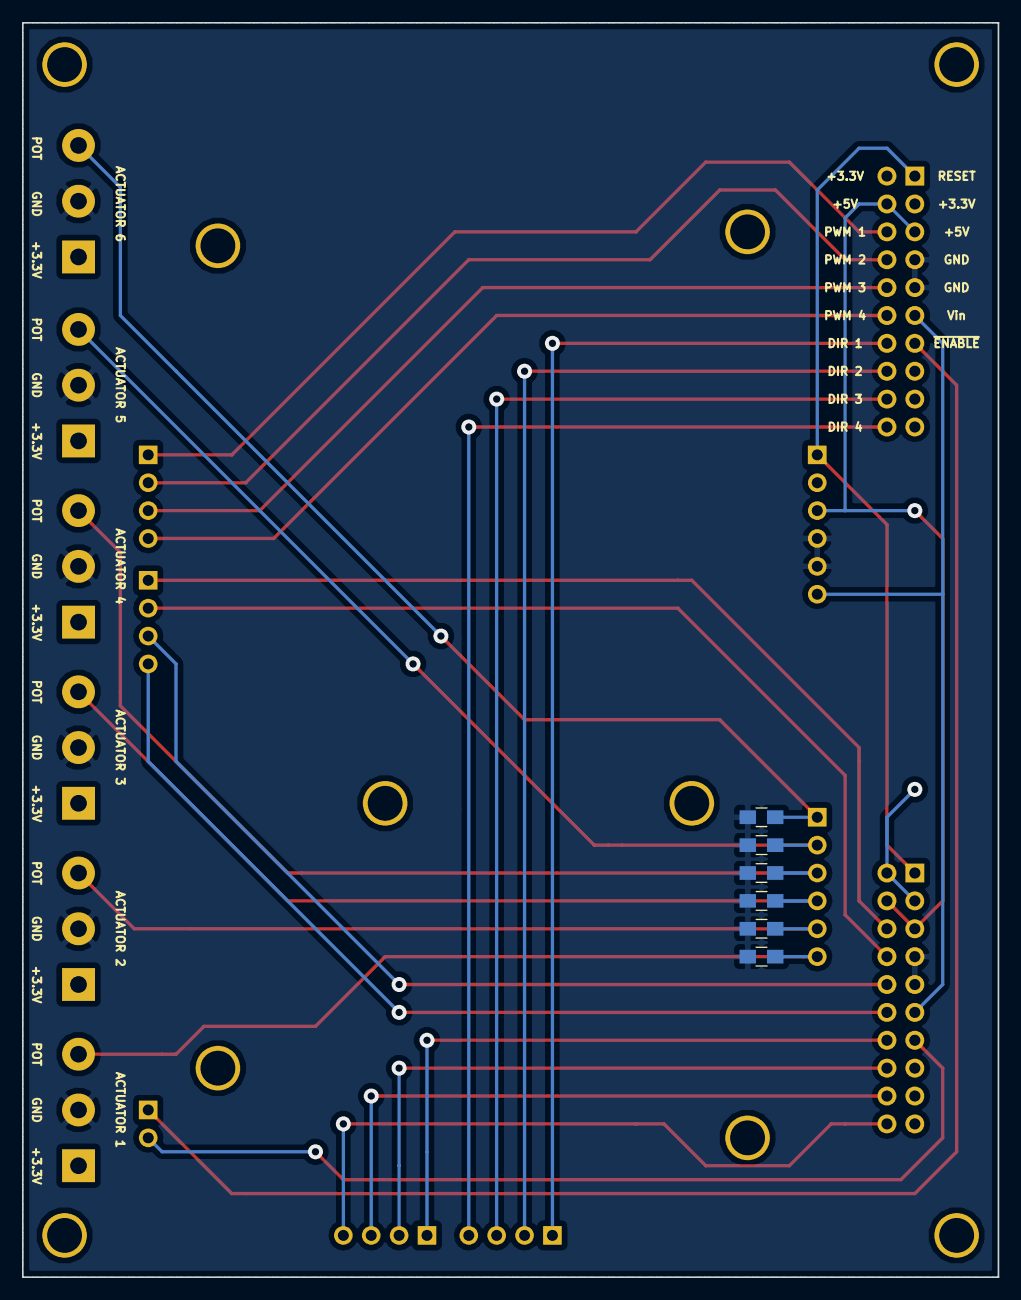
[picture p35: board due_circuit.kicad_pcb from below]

Board: 2 copper layers, 88.9 x 114.3 mm, 20 parts (6 on the bottom side), 27 nets.

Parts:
ACTUATOR_1, ACTUATOR_2, ACTUATOR_3, ACTUATOR_4, ACTUATOR_5, ACTUATOR_6: HEADER_3; TerminalBlock_bornier-3_P5.08mm
C1, C2, C3, C4, C5, C6: 10nF; C_0805_HandSoldering
DIR_1-4, DIR_5-8: HEADER_4; Pin_Header_Straight_1x04_Pitch2.54mm
MULTIMOTO_1, MULTIMOTO_2: HEADER_10x2; IDC-Header_2x10_Pitch2.54mm_Straight
POT_OUT_1: HEADER_6; Pin_Header_Straight_1x06_Pitch2.54mm
PWM_1-4, PWM_5-8: HEADER_4; Pin_Header_Straight_1x04_Pitch2.54mm
UTIL_1: HEADER_6; Pin_Header_Straight_1x06_Pitch2.54mm

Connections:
+3.3V: ACTUATOR_1.1, ACTUATOR_2.1, ACTUATOR_3.1, ACTUATOR_4.1, ACTUATOR_5.1, ACTUATOR_6.1, MULTIMOTO_1.2, MULTIMOTO_1.3, MULTIMOTO_2.2, MULTIMOTO_2.3, UTIL_1.2
+5V: MULTIMOTO_1.4, MULTIMOTO_1.5, MULTIMOTO_2.4, MULTIMOTO_2.5, UTIL_1.3
DIR_1: DIR_1-4.1, MULTIMOTO_1.14
DIR_2: DIR_1-4.2, MULTIMOTO_1.16
DIR_3: DIR_1-4.3, MULTIMOTO_1.18
DIR_4: DIR_1-4.4, MULTIMOTO_1.20
DIR_5: DIR_5-8.1, MULTIMOTO_2.14
DIR_6: DIR_5-8.2, MULTIMOTO_2.16
DIR_7: DIR_5-8.3, MULTIMOTO_2.18
DIR_8: DIR_5-8.4, MULTIMOTO_2.20
GND: ACTUATOR_1.2, ACTUATOR_2.2, ACTUATOR_3.2, ACTUATOR_4.2, ACTUATOR_5.2, ACTUATOR_6.2, C1.2, C2.2, C3.2, C4.2, C5.2, C6.2, MULTIMOTO_1.7, MULTIMOTO_1.9, MULTIMOTO_2.7, MULTIMOTO_2.9, UTIL_1.4, UTIL_1.5
POT_1: ACTUATOR_1.3, C1.1, POT_OUT_1.6
POT_2: ACTUATOR_2.3, C2.1, POT_OUT_1.5
POT_3: ACTUATOR_3.3, C3.1, POT_OUT_1.4
POT_4: ACTUATOR_4.3, C4.1, POT_OUT_1.3
POT_5: ACTUATOR_5.3, C5.1, POT_OUT_1.2
POT_6: ACTUATOR_6.3, C6.1, POT_OUT_1.1
PWM_1: MULTIMOTO_1.6, PWM_1-4.1
PWM_2: MULTIMOTO_1.8, PWM_1-4.2
PWM_3: MULTIMOTO_1.10, PWM_1-4.3
PWM_4: MULTIMOTO_1.12, PWM_1-4.4
PWM_5: MULTIMOTO_2.6, PWM_5-8.1
PWM_6: MULTIMOTO_2.8, PWM_5-8.2
PWM_7: MULTIMOTO_2.10, PWM_5-8.3
PWM_8: MULTIMOTO_2.12, PWM_5-8.4
RESET: MULTIMOTO_1.1, MULTIMOTO_2.1, UTIL_1.1
Vin: MULTIMOTO_1.11, MULTIMOTO_2.11, UTIL_1.6

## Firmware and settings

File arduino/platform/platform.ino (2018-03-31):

// Main Arduino code for a 6-dof Stewart platform.
// Written for the Arduino Due.
//
#include "platform.h"

// Actuator variables
uint8_t pwm[NUM_MOTORS];            // current PWM for each actuator
MotorDirection dir[NUM_MOTORS];     // current direction for each actuator (EXTEND or RETRACT)

// Position variables
int16_t pos[NUM_MOTORS];            // current position (measured by analog read) of each actuator
int16_t input[NUM_MOTORS];          // intermediate input retrieved from the serial buffer
uint16_t desired_pos[NUM_MOTORS];   // desired (user-inputted and validated) position of each actuator

// Feedback variables
int16_t pos_diff;                   // difference between current and desired position
int16_t prop_diff;                  // position difference used for proportional gain
int16_t previous_diff[NUM_MOTORS];  // last position difference for each actuator; for derivative gain
int16_t total_diff[NUM_MOTORS];     // cumulative position difference for each actuator; for integral gain
uint8_t previous_inst[NUM_MOTORS];  // starting/past sample instance for each actuator; for derivative gain
uint8_t current_inst[NUM_MOTORS];   // new/incrementing sample instance for each actuator; for derivative gain
float p_corr;                       // proportional correction for PID
float i_corr;                       // integral correction for PID
float d_corr;                       // differential correction for PID
float corr;                         // final feedback PWM value from PID correction

// Calibration variables
int16_t end_readings[NUM_MOTORS];
int16_t zero_readings[NUM_MOTORS];
bool calibration_valid;

// Time variables (for printing)
unsigned long current_time;         // current time (in millis); used to measure difference from previous_time
unsigned long previous_time;        // last recorded time (in millis); measured from execution start or last print

// Iterator/sum variables
uint8_t motor;                      // used to iterate through actuators by their indexing (0 to NUM_MOTORS - 1)
uint8_t reading;                    // used to iterate through analog reads (0 to NUM_READINGS - 1)
int32_t reading_sum;                // sum of multiple readings to be averaged for a final value


/*
 * Runs once at initialization; set up input and output pins and variables.
 */
void setup()
{
    while (!SerialUSB);

    // Initialize pins
    for (motor = 0; motor < NUM_MOTORS; ++motor)
    {
        pinMode(DIR_PINS[motor], OUTPUT);
        digitalWrite(DIR_PINS[motor], LOW);

        pinMode(PWM_PINS[motor], OUTPUT);
        analogWrite(PWM_PINS[motor], 0);

        pinMode(POT_PINS[motor], INPUT);
    }

    // Initialize actuator enable switches
    pinMode(ENABLE_MOTORS_1, OUTPUT);
    pinMode(ENABLE_MOTORS_2, OUTPUT);
    digitalWrite(ENABLE_MOTORS_1, LOW);
    digitalWrite(ENABLE_MOTORS_2, LOW);

    // For safety, set initial actuator settings and speed to 0
    for (motor = 0; motor < NUM_MOTORS; ++motor)
    {
        total_diff[motor] = 0;
        desired_pos[motor] = 0;
        pwm[motor] = MIN_PWM;
    }

    // Initialize serial communication
    SerialUSB.begin(BAUD_RATE);

    // Run calibration
    calibration_valid = true;
    calibrate();

    // Initialize the current print interval
    #if ENABLE_PRINT
    {
        previous_time = 0;
    }
    #endif // ENABLE_PRINT
}


/*
 * Run tasks in an infinite loop.
 */
void loop()
{
    // Read current actuator positions, map them based on actuator-based scaling from calibration
    for (motor = 0; motor < NUM_MOTORS; ++motor)
    {
        pos[motor] = map(getAverageReading(motor), ZERO_POS[motor], END_POS[motor], MIN_POS, MAX_POS);
    }

    // Parse new serial input if enough is in the buffer (also sets desired position if input is valid)
    if (SerialUSB.available() > INPUT_TRIGGER)
    {
        readSerial();
    }

    // Print actuator information at a given interval
    #if ENABLE_PRINT
    {
        printOutput();
    }
    #endif // ENABLE_PRINT

    // For each actuator, set movement parameters (direction, PWM) and execute motion
    for (motor = 0; motor < NUM_MOTORS; ++motor)
    {
        move(motor);
    }
}


/*
 * Take NUM_READINGS readings of a potentiometer pin and returns the average.
 */
int getAverageReading(uint8_t motor)
{
    reading_sum = 0;
    for (reading = 0; reading < NUM_READINGS; ++reading)
    {
        reading_sum += analogRead(POT_PINS[motor]);
    }
    return reading_sum / NUM_READINGS;
}


/*
 * Move all actuators in a given direction at full PWM.
 */
inline void moveAll(MotorDirection dir)
{
    for (motor = 0; motor < NUM_MOTORS; ++motor)
    {
        digitalWrite(DIR_PINS[motor], dir);
        analogWrite(PWM_PINS[motor], MAX_PWM);
    }
}


/*
 * Read and parse serial input into actuator positions.
 */
inline void readSerial()
{
    // Parse ints from serial
    for (motor = 0; motor < NUM_MOTORS; ++motor)
    {
        input[motor] = SerialUSB.parseInt();
    }

    // Check that inputs are valid
    for (motor = 0; motor < NUM_MOTORS; ++motor)
    {
        if (input[motor] < MIN_POS || input[motor] > MAX_POS)
        {
            return;
        }
    }

    // Set the input as the desired positions
    for (motor = 0; motor < NUM_MOTORS; ++motor)
    {
        total_diff[motor] = 0;  // reset integral feedback given a new target
        desired_pos[motor] = input[motor];
    }
}


/*
 * Print actuator variables over serial at a given interval.
 */
inline void printOutput()
{
    current_time = millis();
    if (current_time - previous_time > PRINT_INTERVAL)
    {
        // Print instance header
        #if ENABLE_PRINT_HEADERS
        {
            SerialUSB.print("<COM>\n");
        }
        #endif // ENABLE_PRINT_HEADERS

        // Print desired position
        #if PRINT_DESIRED_POS
        {
            #if ENABLE_PRINT_HEADERS
            {
                SerialUSB.print("      DESIRED POS: ");
            }
            #endif // ENABLE_PRINT_HEADERS

            for (motor = 0; motor < NUM_MOTORS; ++motor)
            {
                SerialUSB.print(desired_pos[motor]);
                SerialUSB.print(" ");
            }

            SerialUSB.print("\n");
        }
        #endif // PRINT_DESIRED_POS

        // Print current position
        #if PRINT_CURRENT_POS
        {
            #if ENABLE_PRINT_HEADERS
            {
                SerialUSB.print("      CURRENT POS: ");
            }
            #endif // ENABLE_PRINT_HEADERS

            for (motor = 0; motor < NUM_MOTORS; ++motor)
            {
                SerialUSB.print(pos[motor]);
                SerialUSB.print(" ");
            }

            SerialUSB.print("\n");
        }
        #endif // PRINT_CURRENT_POS

        // Print PWM values
        #if PRINT_PWM
        {
            #if ENABLE_PRINT_HEADERS
            {
                SerialUSB.print("      PWM        : ");  // align values wih other entries
            }
            #endif // ENABLE_PRINT_HEADERS

            for (motor = 0; motor < NUM_MOTORS; ++motor)
            {
                SerialUSB.print(pwm[motor]);
                SerialUSB.print(" ");
            }

            SerialUSB.print("\n");
        }
        #endif // PRINT_PWM

        // Print CR to end message block
        #if ENABLE_PRINT_HEADERS
        {
            SerialUSB.print("\r");
        }
        #endif // ENABLE_PRINT_HEADERS

        previous_time = current_time;
    }
}


/*
 * Compute the PID values given the current actuator position, and use them
 * to move the actuator with new direction/PWM values.
 */
inline void move(uint8_t motor)
{
    // Compute the error value
    pos_diff = pos[motor] - desired_pos[motor];

    // Compute error-dependent PID variables
    if (abs(pos_diff) <= POS_THRESHOLD[motor])
    {
        prop_diff = 0;
        total_diff[motor] = 0;
    }
    else
    {
        prop_diff = pos_diff;
        total_diff[motor] += pos_diff;
    }
    if (previous_diff[motor] != pos_diff)
    {
        previous_inst[motor] = current_inst[motor];
        current_inst[motor] = 1;
    }

    // Compute PID gain values
    p_corr = P_COEFF[motor] * prop_diff;
    i_corr = I_COEFF[motor] * total_diff[motor];
    d_corr = D_COEFF[motor] * ((float) pos_diff - previous_diff[motor]) / (current_inst[motor] + previous_inst[motor]);

    // Compute the correction value and set the direction and PWM for the actuator
    corr = p_corr + i_corr + d_corr;
    dir[motor] = (corr > 0) ? RETRACT : EXTEND;  // direction based on the sign of the error
    pwm[motor] = constrain(abs(corr), MIN_PWM, MAX_PWM);  // bound the correction by the PWM limits

    // Move the actuator with the new direction and PWM values
    digitalWrite(DIR_PINS[motor], dir[motor]);
    analogWrite(PWM_PINS[motor], pwm[motor]);

    // Increment sample-dependent PID variables for the next sampling time
    current_inst[motor] += 1;
    previous_diff[motor] = pos_diff;
}


/**
 * Calibration routine run on startup.
 * Extends all actuators, reads extended values, then retracts all, and reads their retracted values.
 */
inline void calibrate()
{
    // Extend all actuators
    for (motor = 0; motor < NUM_MOTORS; ++motor)
    {
        // Start with extension
        digitalWrite(DIR_PINS[motor], EXTEND);
        analogWrite(PWM_PINS[motor], MAX_PWM);
    }
    delay(RESET_DELAY);

    // Stop the extension, get averaged analog readings
    for (motor = 0; motor < NUM_MOTORS; ++motor)
    {
        analogWrite(PWM_PINS[motor], 0);
        end_readings[motor] = getAverageReading(motor);

        // Check if the motors are powered (reading is valid)
        calibration_valid = (abs(end_readings[motor] - END_POS[motor]) < OFF_THRESHOLD);
        if (!calibration_valid)
        {
            break;
        }
    }
    // Retract all actuators
    for (motor = 0; motor < NUM_MOTORS; ++motor)
    {
        digitalWrite(DIR_PINS[motor], RETRACT);
        analogWrite(PWM_PINS[motor], MAX_PWM);
    }
    delay(RESET_DELAY);

    // Stop the retraction, get averaged analog readings
    if (calibration_valid)
    {
        for (motor = 0; motor < NUM_MOTORS; ++motor)
        {
            analogWrite(PWM_PINS[motor], 0);
            zero_readings[motor] = getAverageReading(motor);

            // Check if the motors are powered (reading is valid)
            calibration_valid = (abs(zero_readings[motor] - ZERO_POS[motor]) < OFF_THRESHOLD);
            if (!calibration_valid)
            {
                break;
            }
        }
    }

    // Set the new calibration values if found to be valid
    if (calibration_valid)
    {
        for (motor = 0; motor < NUM_MOTORS; ++motor)
        {
            END_POS[motor] = end_readings[motor];
            ZERO_POS[motor] = zero_readings[motor];
        }
    }

    // Print the calibration result (new max/min values, or a warning)
    #if ENABLE_PRINT_HEADERS
    {
        if (calibration_valid)
        {
            SerialUSB.print("<COM> Finished calibration:\n");

            // Print minimum positions
            SerialUSB.print("      MIN POS: ");
            for (motor = 0; motor < NUM_MOTORS; ++motor)
            {
                SerialUSB.print(ZERO_POS[motor]);
                SerialUSB.print(" ");
            }
            SerialUSB.print("\n");

            // Print maximum positions
            SerialUSB.print("      MAX POS: ");
            for (motor = 0; motor < NUM_MOTORS; ++motor)
            {
                SerialUSB.print(END_POS[motor]);
                SerialUSB.print(" ");
            }
            SerialUSB.print("\n");

            // Print CR to end message block
            SerialUSB.print("\r");
        }

        else
        {
            // Print an error message for calibration failure
            SerialUSB.print("<COM> Failed calibration (using default values).\n");
            SerialUSB.print("      Please verify that the actuators are powered on.\n\r");
        }
    }
    #endif // ENABLE_PRINT
}

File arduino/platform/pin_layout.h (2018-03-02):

// Header file containing hardware configurations for the Arduino Due mapping to the linear actuators.
//
#pragma once

// Direction pins
#define DIR_PIN_1 37
#define DIR_PIN_2 39
#define DIR_PIN_3 41
#define DIR_PIN_4 31
#define DIR_PIN_5 33
#define DIR_PIN_6 35

// PWM pins
#define PWM_PIN_1 11
#define PWM_PIN_2 12
#define PWM_PIN_3 13
#define PWM_PIN_4 8
#define PWM_PIN_5 9
#define PWM_PIN_6 10

// PA-14P potentiometer pins
#define POT_PIN_1 A6
#define POT_PIN_2 A7
#define POT_PIN_3 A8
#define POT_PIN_4 A9
#define POT_PIN_5 A10
#define POT_PIN_6 A11

// Enable for all motors (grouped as such due to different H-bridge controllers)
#define ENABLE_MOTORS_1 24
#define ENABLE_MOTORS_2 25

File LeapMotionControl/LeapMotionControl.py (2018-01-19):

import sys
import serial
import Leap
import numpy as np

# Dependencies: numpy, pyserial

NO_SERIAL = False # used for debugging if no Arduino present
FRAME_RATE = 1 # Number of frames to skip before sending/printing data    

SERIAL_PORT = '/dev/cu.usbmodem1421'
BAUD_RATE = 74880  # found to be the most stable standard rate to avoid board hang

NUM_ACTUATORS = 6

# Base actuator positions (6 1x3 vectors)
BASE_POS = np.matrix([[-246.34, 86.42, 0],
                      [-198.16, 170.38, 0],
                      [198.16, 170.38, 0],
                      [246.34, 86.42, 0],
                      [48.48, -256.80, 0],
                      [-48.48, -256.80, 0]])

# End effector positions (6 1x4 vectors)
END_EFF_POS = np.matrix([[-225.6, -73.26, 0, 1.0],
                         [-49.35, 232.01, 0, 1.0],
                         [49.35, 232.01, 0, 1.0],
                         [225.60, -73.26, 0, 1.0],
                         [176.25, -158.75, 0, 1.0],
                         [-176.25, -158.75, 0, 1.0]])

HOME_POSITION_HEIGHT = 319.0
MIN_ACTUATOR_LEN = 335.0


def assemble_serial_output(actuators):
    """
    Assembles a string to send over serial output given list of actuator positions.

    :param actuators: List of numbers representing desired actuator positions.
    :type actuators: list
    :return: String to send over serial.
    :rtype: str
    """
    s = ""
    for l in actuators:
        s += str(int(l)) + " "

    return s


class LeapListener(Leap.Listener):

    def on_init(self, controller):
        print "Initializing"
        self.frame_count = 0
        if not NO_SERIAL:
            self.ser = serial.Serial(SERIAL_PORT, BAUD_RATE)

    def on_connect(self,controller):
        print "Connected"
    
    def on_disconnect(self, controller):
        print "Disconnected"

    def on_exit(self, controller):
        """
        Called when the listener instance is removed from the controller.
        Also closes the serial connection (if in use).
        """
        print "Exited"
        if not NO_SERIAL:
            self.ser.close()

    def on_frame(self, controller):
        """
        Called when new tracking data arrives.
        """
        frame = controller.frame()
        if len(frame.hands) > 0:
            # Grab rightmost hand
            hand = frame.hands.rightmost

            if hand.is_valid:
                # Get hand position, RPY data
                pos = hand.palm_position

                pitch = hand.direction.pitch
                yaw = hand.direction.yaw
                roll = hand.palm_normal.roll

                # 4x4 affine transform matrix
                transform_matrix = np.matrix([[np.cos(yaw) * np.cos(pitch), np.cos(pitch) * np.sin(yaw), -np.sin(pitch), 0],
                                              [np.cos(yaw) * np.sin(pitch) * np.sin(roll) - np.sin(yaw) * np.cos(roll), np.cos(yaw) * np.cos(roll) + np.sin(roll) * np.sin(yaw) * np.sin(pitch), np.cos(pitch) * np.sin(roll), 0],
                                              [np.cos(yaw) * np.sin(pitch) * np.cos(roll) + np.sin(yaw) * np.sin(roll), -np.cos(yaw) * np.sin(roll) + np.cos(roll) * np.sin(yaw) * np.sin(pitch), np.cos(pitch) * np.cos(roll), 0],
                                              [0, 0, 0, 1]])

                # Multiply transform matrix with end-effector joint position, add position of end-effector, add height of 'home' position to z-coordinate to compensate
                # Equation: transform_matrix * PLATFORM_POSITIONS[i].T + [x, -z, y + home, 0].T = effector_pos
                # Dims:     ( 4 x 4 )           ( 4 x 1 )                 ( 4 x 1 )                ( 4 x 1 )
                actuator_lengths = []
                for i in range(NUM_ACTUATORS):
                    effector_pos = transform_matrix * END_EFF_POS[i].T + np.matrix([pos.x, -pos.z, pos.y + HOME_POSITION_HEIGHT, 0]).T

                    # Get length of extension from min actuator length
                    # Equation: norm(effector_pos - base_pos) - MIN_ACTUATOR_LEN = rel_length
                    # Dims:          ( 3 x 1 )      ( 3 x 1 )      ( 1 x 1 )       ( 1 x 1 )
                    actuator_lengths.append(np.linalg.norm(effector_pos[:3,:] - BASE_POS[i].T) - MIN_ACTUATOR_LEN)

                # Assemble into serial output string
                ser_string = assemble_serial_output(actuator_lengths)

                # Limit output rate, print and send string
                if self.frame_count > FRAME_RATE:
                    print ser_string

                    if not NO_SERIAL:
                        self.ser.write(ser_string)

                    self.frame_count = 0
                else:
                    self.frame_count += 1

def main():

    # Initialize listener and controller
    listener = LeapListener()
    controller = Leap.Controller()

    controller.add_listener(listener)

    # Required to keep tracking going
    raw_input("Press enter to exit...\n")

    controller.remove_listener(listener)

if __name__ == "__main__":
    main()

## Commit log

2017-11-05 Recalibrated actuators, fixed mapping of motor position values
2017-11-12 Fixed some bugs, should be somewhat working now (not tested with serial yet)
    [LeapMotionControl.py]
2017-11-14 Ignore compiled Arduino hex from Sublime
2018-01-04 Ported code in master branch to Arduino Due
2018-01-28 Separate Leap Motion files into Windows/Mac due to dependency issues on Windows
    [LeapMotionControl.py]
2018-01-28 Add serial/timeout changes from threading branch to the Leap Motion Python script
2018-01-30 Changed serial/line-endings to fix issues on Windows
    [LeapMotionControl.py]
2018-02-06 Rename GUI elements, got include dependencies and exit button working
2018-02-22 Register QVector in GUI for Leap Motion error
    [main.cpp]
2018-02-22 Add refactored Arduino files (clean up code, update calibration values)
2018-02-22 Add early PID code; yet to be tested and tuned
2018-02-26 Fix bug in serial int parsing
    [platform.ino]
2018-03-04 Refactor Arduino code for PID control, add performance script to measure positional accuracy
2018-03-13 Switch fields/sliders to separate vectors to fix actuator mismatch from QMap ordering
2018-03-16 Added calibration to startup routine
2018-03-28 Clean up and improve logging for Arduino code
2018-03-29 Update calibration and PID tuning
2018-03-30 Remove old Arduino files, wait for serial connection before setup/calibration
2018-03-30 Add design, schematic, and gerber files for electronics/PCBs
    [controller_circuit.kicad_pcb, controller_circuit.sch, due_circuit.kicad_pcb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]
2018-03-31 Adjust platform height and actuator lengths to physical dimensions, remove Help menu as it is currently unused
2018-03-31 Adjust PID based on script results
2018-04-04 Added solidworks files, DXF files, mechanical drawing files and drawing pdfs.
    [MotorPanel.SLDDRW, MotorPanel.SLDPRT, MotorPanel2.DXF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]
2018-04-06 Added assembly instructions
2018-04-07 Temporarily remove mechanical folder for renaming
    [MotorPanel.SLDDRW, MotorPanel.SLDPRT, MotorPanel2.DXF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]
2018-04-07 Re-add mechanical files from last commit with correct directory
    [MotorPanel.SLDDRW, MotorPanel.SLDPRT, MotorPanel2.DXF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]
2018-04-07 Add wiring instructions to README.md
2018-04-14 Add PCB design section to wiki
2018-05-03 Update README with wiring pics, ToC
